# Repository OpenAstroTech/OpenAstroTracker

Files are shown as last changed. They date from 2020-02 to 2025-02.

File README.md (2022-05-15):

# The OpenAstroTracker:



https://youtu.be/9MNLAIyqGoA

A cheap 3D printed tracking, GoTo and autoguiding mount for DSLR astrophotography.

# [OpenAstroTracker Kits Now Available!](https://shop.openastrotech.com/products/openastrotracker-diy-kit)

# Links
 - [Software](https://github.com/OpenAstroTech/OpenAstroTracker/releases)
 - [Reddit](https://www.reddit.com/r/OpenAstroTech/)
 - [Discord](https://discord.gg/TmEfSNaBnB)
 - [Guides](https://www.reddit.com/r/OpenAstroTech/comments/gc4pmr/all_current_guides/)
 - [Wiki](https://wiki.openastrotech.com/)
 - [OpenAstroGuider](https://www.thingiverse.com/thing:4181640) Autoguiding Addon
 - [Community-made Addons](https://www.thingiverse.com/openastrotech/collections/things-for-the-openastrotracker) I'll add things to this Collection, if you made something, send me a message.
 - [My Images](https://www.instagram.com/fabianuehleke/)
 - [Community Images](https://www.flickr.com/groups/14697674@N24/)

##

**Use the [Printed Parts Chooser](https://docs.google.com/spreadsheets/d/1uDw7Jag2HRKztMPO7b06qFRg1eezGeb0IxJh84-QEao/edit?usp=sharing)**

# Like this Project?
**[Buy me and the devs a coffee!](https://www.paypal.com/donate/?hosted_button_id=HMY3H3PTGPFXN)**

If you would be interested in buying the tracker as a printed kit, head over to [this site](https://openastrotech.com/products/)

##

# Check out our [Wiki](https://wiki.openastrotech.com/) for all the guides!

This is the Repo for CAD and STL files. The other Repo's are:
 - [/OpenAstroTracker-Firmware](https://github.com/OpenAstroTech/OpenAstroTracker-Firmware) for OAT Arduino Firmware
 - [/OpenAstroTracker-Desktop](https://github.com/OpenAstroTech/OpenAstroTracker-Desktop) for OAT ASCOM and OATcontrol
 - [/OpenAstroTracker-Addons](https://github.com/OpenAstroTech/OpenAstroTracker-Addons) for OAT Hardware addons 
 - [/OpenAstroTracker-Apps](https://github.com/OpenAstroTech/OpenAstroTracker-Apps) (WIP) Mobile Apps

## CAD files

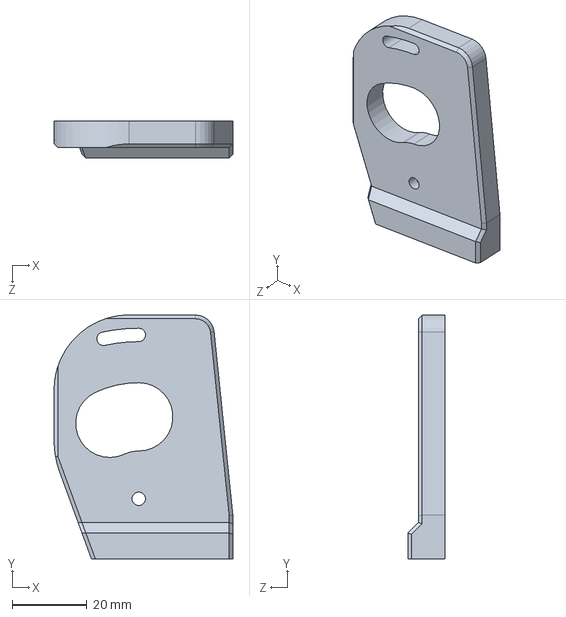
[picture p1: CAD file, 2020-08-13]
CAD/Solidworks/16_DEC_motor_mount_v8_low_NEMA14.SLDPRT
47.9 x 65.4 x 10.0 mm

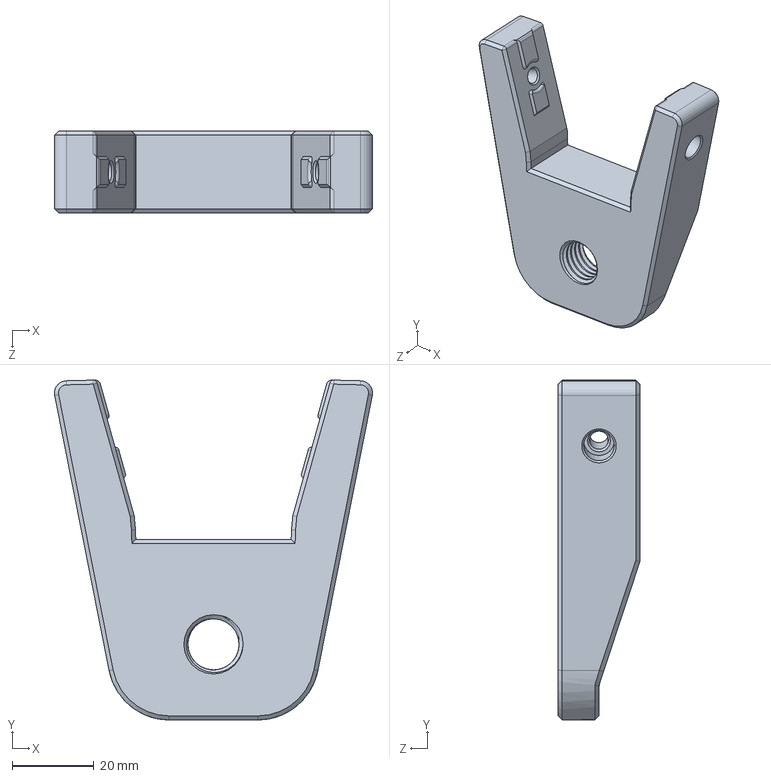
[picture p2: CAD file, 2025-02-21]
CAD/Solidworks/2020base/M14_mount_rear_2020base_v4.SLDPRT
77.8 x 83.2 x 20.0 mm

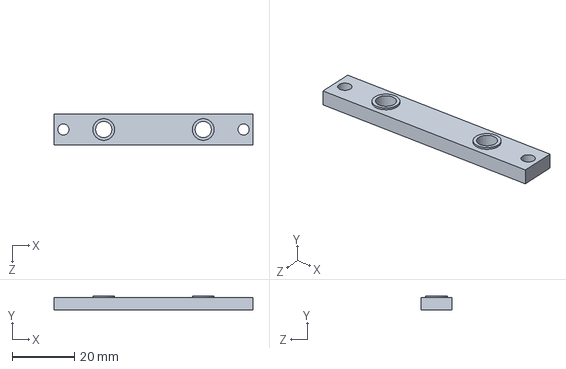
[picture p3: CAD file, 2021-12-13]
CAD/Solidworks/All Latitudes/16.1_DEC_idler_bracket_v1_NEMA.SLDPRT
64.0 x 4.50 x 10.0 mm

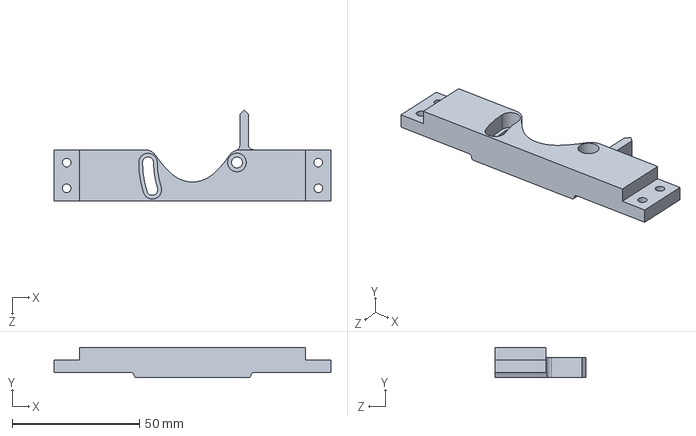
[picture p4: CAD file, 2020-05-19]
CAD/Solidworks/Printed Base & Printed Camera mount/For 200x200 printers/22_RAmotor_mount_low_v4_200x200.SLDPRT
109.0 x 12.0 x 35.9 mm

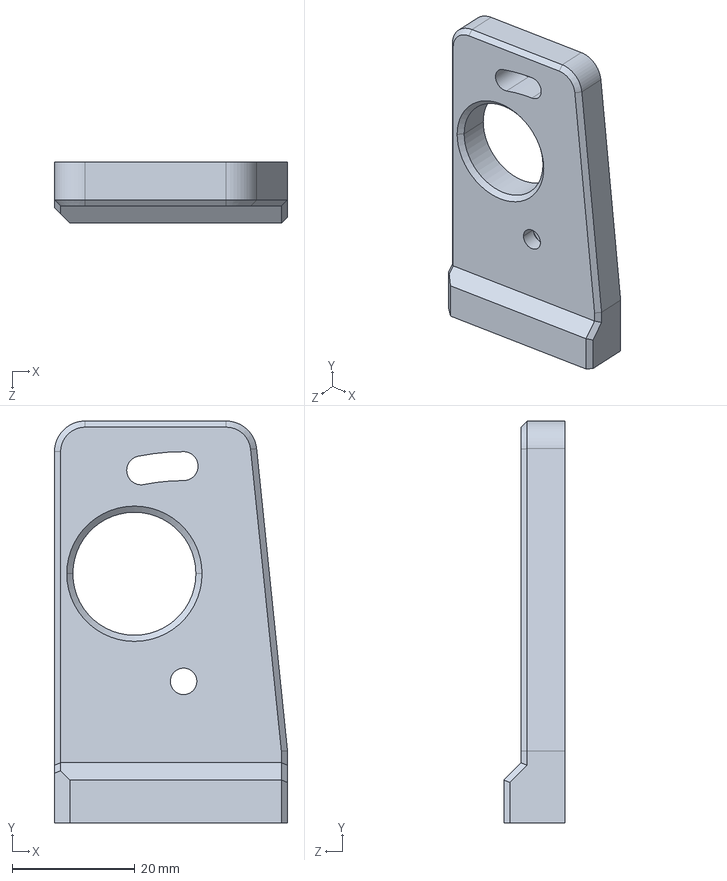
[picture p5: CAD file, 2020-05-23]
CAD/STEP/16_DEC_motor_mount_v7_low.step
37.9 x 65.4 x 10.0 mm

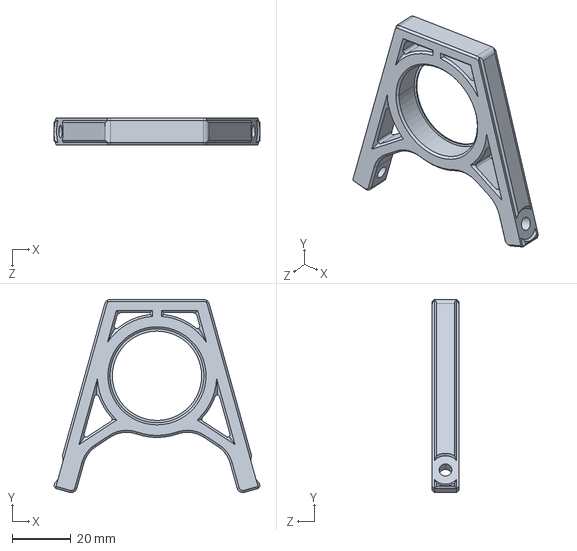
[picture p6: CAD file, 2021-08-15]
CAD/STEP/2020base/b2_level holder_31mm.STEP
69.9 x 65.6 x 9.00 mm

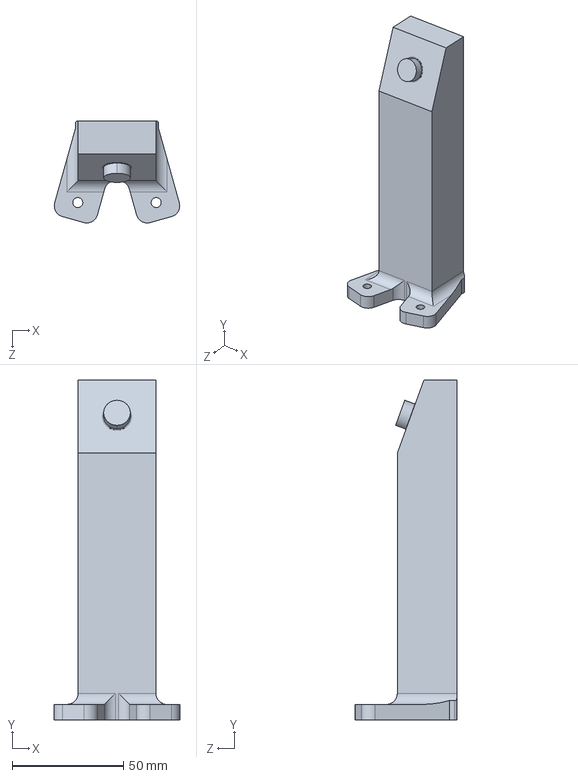
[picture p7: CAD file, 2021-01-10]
CAD/STEP/20deg/02_angle_20deg_2020base.step
56.5 x 152.9 x 45.8 mm

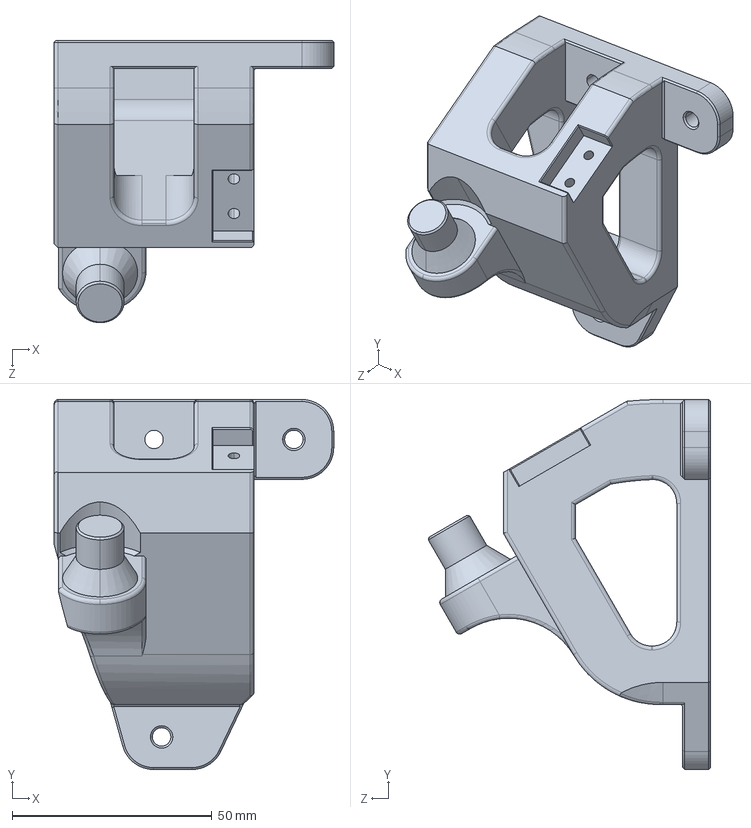
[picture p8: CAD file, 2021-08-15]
CAD/STEP/30deg/04_rollmount right_30°_v6_2020base.STEP
70.0 x 92.6 x 70.7 mm

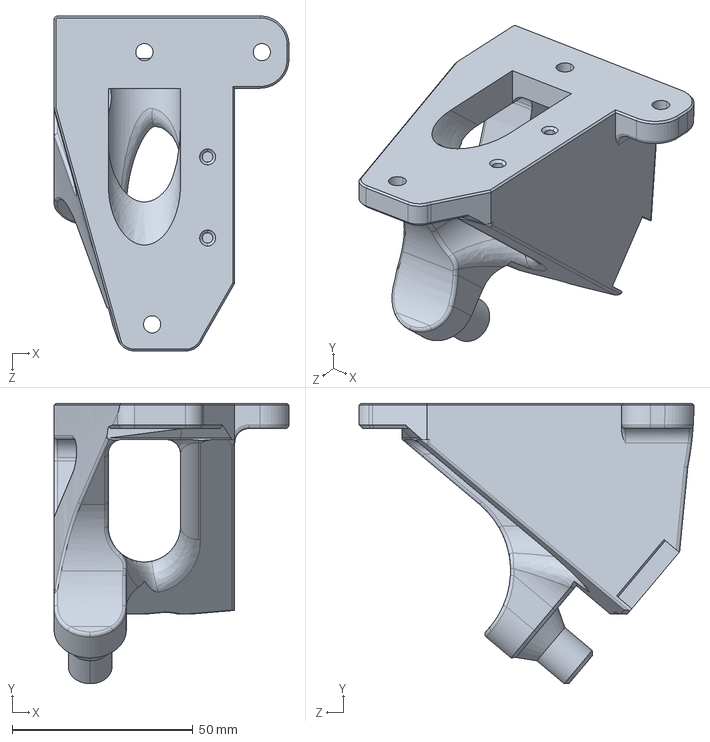
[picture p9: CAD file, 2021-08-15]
CAD/STEP/40deg/04_rollmount left_40°_v6_2020base.STEP
65.0 x 77.6 x 92.7 mm

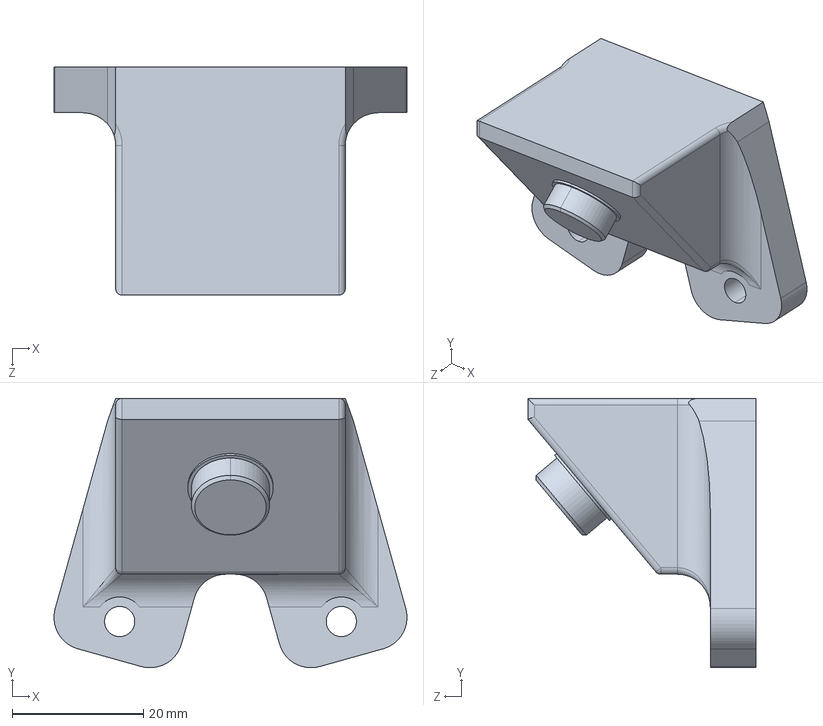
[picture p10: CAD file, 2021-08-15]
CAD/STEP/50deg/02_angle_50deg_v4_2020base.STEP
53.8 x 41.1 x 34.8 mm

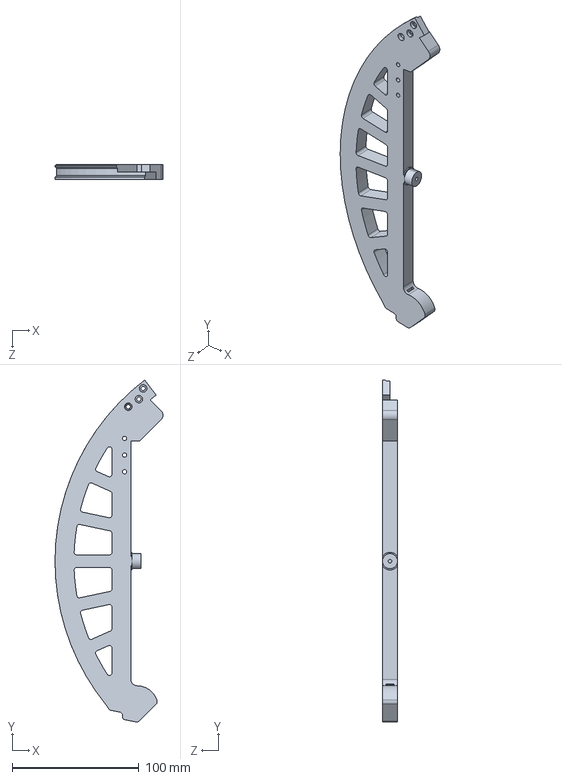
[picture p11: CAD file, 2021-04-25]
CAD/STEP/All Latitudes/For 200x200 Printers/06a_splitring_part1_v4f_200x200.STEP
85.3 x 270.3 x 12.0 mm

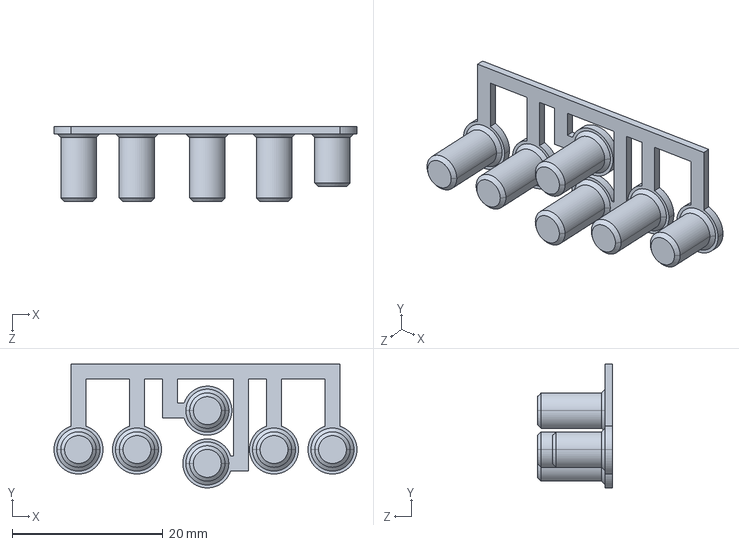
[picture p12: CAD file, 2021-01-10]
CAD/STEP/Arduino Mega Handcontroller/c4_buttons.step
40.2 x 16.4 x 10.0 mm

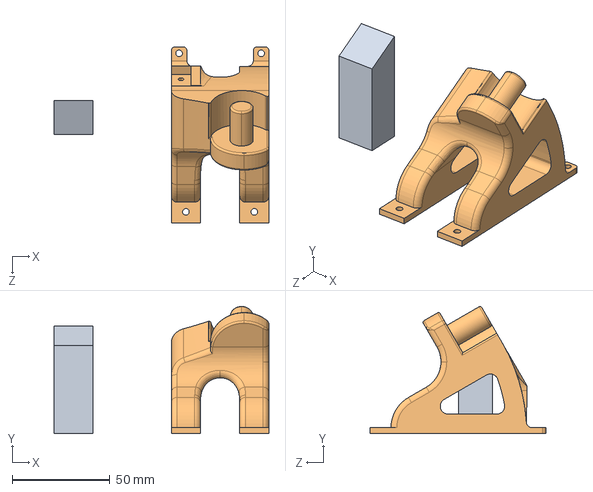
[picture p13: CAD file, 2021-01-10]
CAD/STEP/Printed Base & Printed Camera mount/04_rollmount left_30°_v3.step
110.0 x 65.0 x 90.3 mm

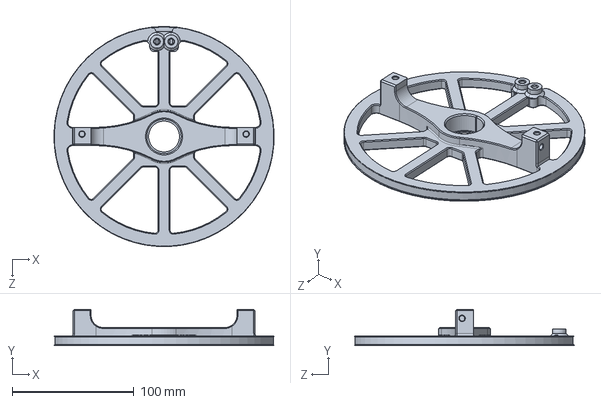
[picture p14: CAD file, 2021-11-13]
CAD/STEP/Universal mount/u3_drivedisc_DEC_unimount_v3_TI.STEP
181.0 x 30.0 x 181.2 mm

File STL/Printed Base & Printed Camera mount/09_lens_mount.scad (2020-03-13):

//$fn=10;

//lens_diameter = 62;

diam1 = 69.5;
diam2 = 69.5;
high1 = 6;


diam3 = 62.5;
diam4 = 62.5;
high2 = 25;

high3 = 0;
diam5 = 0;
diam6 = 0;

length = 30; //reduce this if needed

/*union() {
translate([0,0,20]) cube([(diam1/2)+5,100,10]);
mirror([1,0,0]) translate([0,0,20]) cube([(diam1/2)+5,100,10]);
mirror([0,1,0]) translate([0,0,20]) cube([(diam1/2)+5,100,10]);
mirror([1,0,0])mirror([0,1,0]) translate([0,0,20]) cube([(diam1/2)+5,100,10]);
}*/

difference (){
difference (){
difference (){
union (){
    cylinder (h=30,d=diam1+10,$fn=512);
    cube([67,15.5/2,30]);
    mirror([1,0,0]) cube([67,15.5/2,30]);
    mirror([0,1,0]) cube([67,15.5/2,30]);
    mirror ([1,0,0])mirror([0,1,0]) cube([67,15.5/2,30]);
}
}
union () {
translate([0,0,-0.001]) cylinder(high1+0.1,d1=diam1,d2=diam2,$fn=512);
translate([0,0,high1-0.01]) cylinder(high2+0.1,d1=diam3,d2=diam4,$fn=512);
translate([0,0,high1+high2-0.02]) cylinder(high3+0.1,d1=diam5,d2=diam6,$fn=512);
    
union() {
translate([0,0,length+0.001]) cube([(diam1/2)+4.2,100,100]);
mirror([1,0,0]) translate([0,0,length+0.001]) cube([(diam1/2)+4.2,100,100]);
mirror([0,1,0]) translate([0,0,length+0.001]) cube([(diam1/2)+4.2,100,100]);
mirror([1,0,0])mirror([0,1,0]) translate([0,0,length+0.001]) cube([(diam1/2)+4.2,100,100]);
}
    
}
}
cube([150,1,61],center=true);
translate ([67-15,5.9/2+4.45,15/2]) hex(5.9,5.9);
translate ([67-15,5.9/2+4.45,30-15/2]) hex(5.9,5.9);
translate ([-67+15,5.9/2+4.45,15/2]) hex(5.9,5.9);
translate ([-67+15,5.9/2+4.45,30-15/2]) hex(5.9,5.9);
translate([67-15,8,15/2]) rotate([90,0,0]) cylinder(h=20,d=3.4,$fn=512);
translate([67-15,8,30-15/2]) rotate([90,0,0]) cylinder(h=20,d=3.4,$fn=512);
translate([-67+15,8,15/2]) rotate([90,0,0]) cylinder(h=20,d=3.4,$fn=512);
translate([-67+15,8,30-15/2]) rotate([90,0,0]) cylinder(h=20,d=3.4,$fn=512);
translate([67-15,-3.95,15/2]) rotate([90,0,0])cylinder (h=5,d=5.8,$fn=512);
translate([67-15,-3.95,30-15/2]) rotate([90,0,0])cylinder (h=5,d=5.8,$fn=512);
translate([-67+15,-3.95,15/2]) rotate([90,0,0])cylinder (h=5,d=5.8,$fn=512);
translate([-67+15,-3.95,30-15/2]) rotate([90,0,0])cylinder (h=5,d=5.8,$fn=512);
}


module hex(wid,height){
hull(){
cube([wid/1.7,wid,height],center = true);
rotate([0,120,0])cube([wid/1.7,wid,height],center = true);
rotate([0,240,0])cube([wid/1.7,wid,height],center = true);
}
}

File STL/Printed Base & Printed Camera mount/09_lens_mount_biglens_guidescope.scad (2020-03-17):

//$fn=10;

//lens_diameter = 62;

diam1 = 69.5; //[0:0.1:120]
diam2 = 65.5; //[0:0.1:120]
high1 = 6; //[0:0.1:30]


diam3 = 62.5; //[0:0.1:120]
diam4 = 62.5; //[0:0.1:120]
high2 = 25; //[0:0.1:30]

diam5 = 0; //[0:0.1:120]
diam6 = 0; //[0:0.1:120]
high3 = 0; //[0:0.1:30]

/* [Hidden] */
dmax = max(diam1,diam2,diam3,diam4,diam5,diam6);
gy = sqrt(max(dmax*dmax/4-41.9*41.9,20*20))+8;
gx_1 = sqrt((dmax/2+2.5)*(dmax/2+2.5)-gy*gy);
gx_2 = sqrt((dmax/2+2.5)*(dmax/2+2.5)-7.5*7.5);
gx_3 = max(sqrt((dmax/2+5)*(dmax/2+5)-7.5*7.5),57.1);

$fn=512;

difference (){
difference (){
difference (){
union (){
    cylinder (h=30,d=diam1+10);
    cube([91.3,15.5/2,30]);
    mirror([1,0,0]) cube([91.3,15.5/2,30]);
    mirror([0,1,0]) cube([91.3,15.5/2,30]);
    mirror ([1,0,0])mirror([0,1,0]) cube([91.3,15.5/2,30]);
    translate([0,0,6]) linear_extrude(height=18) polygon(points=[[-gx_1,-gy],[-55.1,-gy],[-57.1,-gy+2],[-gx_3,-7.49],[-gx_2,-7.49]]);
    mirror([1,0,0]) translate([0,0,6]) linear_extrude(height=18) polygon(points=[[-gx_1,-gy],[-55.1,-gy],[-57.1,-gy+2],[-gx_3,-7.49],[-gx_2,-7.49]]);
}
}
union () {
translate([0,0,-0.001]) cylinder(high1+0.1,d1=diam1,d2=diam2);
translate([0,0,high1-0.01]) cylinder(high2+0.1,d1=diam3,d2=diam4);
translate([0,0,high1+high2-0.02]) cylinder(high3+0.1,d1=diam5,d2=diam6);
}
}
cube([200,1,61],center=true);
translate ([91.3-15,5.9/2+4.45,15/2]) hex(5.9,5.9);
translate ([91.3-15,5.9/2+4.45,30-15/2]) hex(5.9,5.9);
translate ([-91.3+15,5.9/2+4.45,15/2]) hex(5.9,5.9);
translate ([-91.3+15,5.9/2+4.45,30-15/2]) hex(5.9,5.9);
translate([91.3-15,8,15/2]) rotate([90,0,0]) cylinder(h=20,d=3.4);
translate([91.3-15,8,30-15/2]) rotate([90,0,0]) cylinder(h=20,d=3.4);
translate([-91.3+15,8,15/2]) rotate([90,0,0]) cylinder(h=20,d=3.4);
translate([-91.3+15,8,30-15/2]) rotate([90,0,0]) cylinder(h=20,d=3.4);
translate([91.3-15,-3.95,15/2]) rotate([90,0,0])cylinder (h=5,d=5.8);
translate([91.3-15,-3.95,30-15/2]) rotate([90,0,0])cylinder (h=5,d=5.8);
translate([-91.3+15,-3.95,15/2]) rotate([90,0,0])cylinder (h=5,d=5.8);
translate([-91.3+15,-3.95,30-15/2]) rotate([90,0,0])cylinder (h=5,d=5.8);
translate([-47,-gy+3,15]) cube([10.2,10,8.2],center=true);
translate([47,-gy+3,15]) cube([10.2,10,8.2],center=true);
}


module hex(wid,height){
hull(){
cube([wid/1.7,wid,height],center = true);
rotate([0,120,0])cube([wid/1.7,wid,height],center = true);
rotate([0,240,0])cube([wid/1.7,wid,height],center = true);
}
}

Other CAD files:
CAD/STEP/All Latitudes/11.1_DEC_idler_bracket_v1_NEMA.STEP
STL/2020 Base/b2_level holder_60mm.STL
STL/20deg/04_rollmount right_20°_v5_2020base_TI.STL
STL/30deg/04_rollmount right_30°_v6_2020base_TI.STL
STL/Printed Base & Printed Camera mount/09_lens_mount_biglens.scad
CAD/STEP/03_polemount_6801.step
CAD/STEP/10.1_pole_v2.step
CAD/STEP/10_pole_20deg.step
CAD/STEP/10_pole_30deg.step
CAD/STEP/10_pole_40deg.step
CAD/STEP/10_pole_50°.step
CAD/STEP/10_pole_50°_v2.step
CAD/STEP/11a_splitring_part1_timingbelt.step
CAD/STEP/11a_splitring_part1_v2.step
CAD/STEP/11b_splitring_part2_v2.step
CAD/STEP/11c_splitring_part3_timingbelt.step
CAD/STEP/11c_splitring_part3_timingbelt1.step
CAD/STEP/11c_splitring_part3_v2.step
CAD/STEP/16_DEC_motor_mount_v6.step
CAD/STEP/16_DEC_motor_mount_v6_low.step
CAD/STEP/2020base/16_NEMA_electronicsbox.step
CAD/STEP/2020base/16_NEMA_electronicsbox_lid.step
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

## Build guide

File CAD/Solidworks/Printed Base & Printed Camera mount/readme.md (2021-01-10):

Numberation on these parts may differ from the STLs

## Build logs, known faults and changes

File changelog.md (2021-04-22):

# Changelog

## Parts
22.04.2021
 - Updated 14_RAmotor_mount_NEMA_down to v4, adding adjustment for belt tension and making _up obsolete. 
 - Added 14_RAmotor_mount_NEMA_down_SngleRAring_v4 for the single piece RA Rings.
 - Updated 05_pole to v5, adding stoppers for upcoming sensorless homing with TMC2209 builds.

20.05.2020
 - see [this post](https://www.reddit.com/r/OpenAstroTech/comments/gnjsvu/a_whole_bunch_of_updated_parts/)

10.04.20
 - updated the files for 200x200 printers with the v2 ring

17.03.2020

 - updated parts 6a,b,c and 14 to v2
 - added klwill1192's lens adapter for big lenses with the guidescope
 Please see the [update post](https://www.reddit.com/r/OpenAstroTech/comments/fkcdho/improvements_to_the_splitring_design_and/) 

13.03.2020

 - added adaptions of parts 11 and 14 (the motor mounts) with the addendum "_low". These will fit with purchased GT2 pulleys.
 - updated the lens ring SCAD. It has a new value "length" for lenses that have little space to mount it.

10.03.2020

 - added 01a, 01b, 06a, 06c adaptions to fit into 200x200 printers
 - updated part 10 to fit tighter with the camera mount, part 08

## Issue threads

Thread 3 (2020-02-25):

SCAD files

BenJuan26, 2020-02-25:
This repo doesn't seem to have the SCAD files mentioned in the readme. I do see that they're on Thingiverse. Should they be added here?

BenJuan26, 2020-02-25:
Found them, in `/STL/All latitudes`. Just another reminder that GitHub's search is garbage.

Closed 2020-02-25.

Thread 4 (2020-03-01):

Assemply instructions

crami, 2020-03-01:
Hi
Could you probably post some assembly instructions or some close-up Photos of your assembled OpenAstroTracker to make assembly easier?

Thanks
  Matthias

threalboss, 2020-03-06:
He is currently working on revising the build guide. Keep up to date on r/openastrotech https://www.reddit.com/r/OpenAstroTech/

OpenAstroTech, 2020-03-28:
have been added

Closed 2020-03-28.

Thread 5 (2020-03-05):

Arduino Code

ztwillis, 2020-03-05:
In the Calculations file in the Arduino code the pins were different than those in Init:
I believe this should be what it reads:

if (DECheat == 1) {
  stepperDEC.enableOutputs();
  digitalWrite(15, HIGH);
  digitalWrite(16, HIGH);
  digitalWrite(17, HIGH);
  digitalWrite(18, HIGH);

Also when I enter my HA from based on Polaris in in stellarium the declination axis(initial position starting perpendicular to RA axis) goes nearly 180 degrees when I enter my HA and go to the Polaris tab and select it.  Thanks in advance!

OpenAstroTech, 2020-03-05:
> different than those in Init

oh right thanks, i changed it

> goes nearly 180 degrees when I enter my HA and go to the Polaris tab and select it

Thats weird, that cant happen unless you entered some coordinates before using the POL menu

ztwillis, 2020-03-05:
Honestly it's probably user error, mostly I just wanted to let you know about the Arduino code, thanks for the quick response and all of the work you're doing!

Closed 2020-03-05.

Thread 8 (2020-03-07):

DEC guiding imprecise

OpenAstroTech, 2020-03-07:
because

a) DEC stepper not precise enough. Could be improved by half-stepping

b) Declination axis unbalanced with guidescope attached. Could be solved by adding counterweights

OpenAstroTech, 2020-03-19:
After further testing, i dont think DEC guiding will ever be precise. Even a single halfstep is roughly one arcmin of movement which is really borderline for ~200mm lenses but not precise enough for higher focal lengths

OpenAstroTech, 2020-08-20:
DEC guiding is working with NEMA stepper on DEC axis

Closed 2020-08-20.

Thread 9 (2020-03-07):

No guidescope attachment for _biglens

OpenAstroTech, 2020-03-07:

klwill1192, 2020-03-16:
Here's my first cut at adding the guide scope mount to the lens mount.

[09_lens_mount_biglens_guidescope.zip](https://github.com/OpenAstroTech/OpenAstroTracker/files/4335575/09_lens_mount_biglens_guidescope.zip)

OpenAstroTech, 2020-03-17:
added!

Closed 2020-03-17.

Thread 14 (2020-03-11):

Button

tomv79, 2020-03-11:
The left button does not switch throught the menues.
It has the same effect as the down button.
Sometimes the left button switches the menue.

OpenAstroTech, 2020-03-11:
Go to the second tab of the code "a_inits" and find line 36 "if (adc_key_in < 600)  return btnLEFT;"

Try if changing the value in that line to 700 or 800 fixes it

tomv79, 2020-03-11:
Yes the left button now works.
But the select button seem to be the left now.

OpenAstroTech, 2020-03-11:
Try increasing its value in the code till it works

tomv79, 2020-03-12:
I have make following changes that works for me well!!

if (adc_key_in > 1000) return btnNONE;
  if (adc_key_in < 20)   return btnRIGHT;
  if (adc_key_in < 150)  return btnUP;
  if (adc_key_in < 300)  return btnDOWN;
  if (adc_key_in < 500)  return btnLEFT;
  if (adc_key_in < 700)  return btnSELECT;

now the keys works fine!

OpenAstroTech, 2020-03-13:
Great! I'll mention this in the upcoming troubleshooting guide, i think some of the LCDs need different values.

Gonna close this

Closed 2020-03-13.

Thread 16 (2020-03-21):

BUG : RASteps not being correctly converted to float in c_buttons.ino

EorEquis, 2020-03-21:
Current line 8 is
`onehour = (float(RAsteps / 288)) * RevSteps;`

Which leave RASteps as an int  (this produces /u/mxpwr60's comment that 288 is the "lower limit" as seen [here](https://old.reddit.com/r/OpenAstroTech/comments/fmiwwz/calibration/), since dividing any int < 288 by 288 returns 0.

It also results in the RA Rate being impossible to set as described in the setup/calibration instructions, since only RASteps values that are multiples of 288 (288, 576, etc) will produce any change in the value of onehour.

I believe code should be
`onehour = (float(RAsteps) / 288) * RevSteps;`

Have made this change in my mount, and see RA calibration results as expected.

OpenAstroTech, 2020-03-28:
forgot to close it

Closed 2020-03-28.

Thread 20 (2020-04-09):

Use common 608 bearings

christoph1703, 2020-04-09:
It would be great to use the common 608 bearings instead of the 12mm ID bearings required now. The price and availability are much better.
I modified the stl files myself before printing, but I don't have access to SolidWorks, so I can't contribute updated files. I'd be happy to help otherwise if needed.
Thanks for providing this thing for free!

andre-stefanov, 2020-06-11:
You can use the .step files for the remixing and later export if for solidworks in e.g. Fusion 360

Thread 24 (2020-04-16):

missing CAD Files

regularUsername, 2020-04-16:
STEP and Solidworks files for **02_angle_30deg** are missing

OpenAstroTech, 2020-04-16:
I have no idea how that happened, but i added them. Thanks!

Closed 2020-04-16.

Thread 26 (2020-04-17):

V1.6 not compiling

raminnobari, 2020-04-17:
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
V1.6. not compiling properly. Errors are located in "d-calulation" and "f-printout" files.
I have no issues with v1.4.5 ...

Am I doing something wrong ?!

raminnobari, 2020-04-17:
1.6.25 compiles just fine. "d-calulation" and "f-printout"  are already gone.

OpenAstroTech, 2020-04-17:
There were accidentally some wrong files in the initial upload for 1.6.25. I reuploaded the code, it should work now with the latest release

raminnobari, 2020-04-17:
perfect

Closed 2020-04-17.

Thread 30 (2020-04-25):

GoTo not working for negative DEC

StandaB, 2020-04-25:
Navigating to POI M42 Orion nebula moves OAT to DEC 90°22' instead of -5°22'. It seems that in _struct PointOfInterest_ using "byte degreeDEC;" is problematic since _byte_ is unsigned. Using _int degreeDEC_ solved this for me

nice project though. I made a slight modification to use A4988 stepper drivers with microstepping to see if it is possible to have smoother tracking. Just waiting for a clear sky now :)

andre-stefanov, 2020-12-13:
Thx! Fixed in e4f2c06743984873fc060b9975149918a24d1c0c

Closed 2020-12-13.

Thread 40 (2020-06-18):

LCD Keypad buttons misbehaving

scoutstang, 2020-06-18:
I just wanted to report an issue I ran into getting my new OAT build up and running. With the electronics hooked up and the latest firmware loaded, some of my buttons were misbehaving. Both the Left and Select buttons were acting like Select and the Down button was acting like Left.

I was able to enable LCD_BUTTON_TEST in Globals.hpp to see the output of my buttons and then change the cutoff values accordingly in the checkKey () part of Utility.hpp. I changed the cutoffs to 50/300/500/700/950. Now the buttons respond correctly.

For the record, I am using firmware 1.7.04 with a Mega 2560 clone (Sunfounder) and the DFRobot LCD Kaypad Shield v1.1. They key diagnostic is reporting: 0-Right, 205-Up, 405-Down, 623-Left, 824-Select, and 1023-None.

Looking forward to clear skies so I can try it out soon!

andre-stefanov, 2020-12-13:
Thanks for that information. We are indeed seeing this issues from time to time because the LCD Keypad shields seem to differ in terms of voltages on each button. Our proposed fix is exactly what you did. I will add this information to the wiki so maybe someone can look it up if he faces same problem.

Closed 2020-12-13.

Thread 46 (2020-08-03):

OATcontrol crashing on startup

BenJuan26, 2020-08-03:
I've downloaded the latest release and extracted OATcontrol. When I try to run `OATControl.exe`, it crashes instantly; no error message, no error report, etc. I attached Visual Studio to the `.exe` and got a bit more information. It seems to be a registry access permission denied. Here is the stack trace:

```
 at ASCOM.Utilities.RegistryAccess.OpenSubKey(RegistryKey ParentKey, String SubKeyName, Boolean Writeable, RegWow64Options Options)\r\n   at ASCOM.Utilities.RegistryAccess.NewCode(Boolean p_IgnoreChecks)
```

And the accompanying message is:

```
OpenSubKey: Exception encountered opening key - Result: 0x5
```

I can probably build from source but I thought it important to point out that the release is crashing for me.

ClutchplateDude, 2020-08-03:
Do you have the latest ASCOM installed (I think 6.2) ?

BenJuan26, 2020-08-03:
That was the issue. I was getting my computers confused and didn't have ASCOM installed on this one. Still, catching the exception would probably be a good idea so that other people know what the problem is.

ClutchplateDude, 2020-08-03:
I think this might be too early to catch an exception. The program won't even start up if the dependencies are missing. Did you have to see any OATControl code in the stack when you looked at that exception?

BenJuan26, 2020-08-03:
> I think this might be too early to catch an exception.

I think you're right. There was very little info available, and I didn't see an OATcontrol file or line number mentioned anywhere. It complained about one of the constructors throwing an exception, but I don't recall whether it was OATcontrol-specific or some internal .NET class. I don't have the report handy anymore, and now that I've installed ASCOM I won't be able to reproduce it.

ClutchplateDude, 2020-08-03:
My problem also :-)

Closed 2020-08-03.

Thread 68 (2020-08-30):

Wrong Serial interface for DEC?

stone17, 2020-08-30:
https://github.com/OpenAstroTech/OpenAstroTracker/blob/d383d151e34142fe88fd5ae8a6d664c53c0af1c6/Software/Arduino%20code/OpenAstroTracker/Configuration_pins.hpp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

This should be Serial2?

My DEC motor doesnt work properly if this is set to Serial3.

pay4nothing, 2020-10-23:
Hi @Stone17,

thank you for your comment. I just had a weird behavor of the DEC axis with slipping and non holding the position. I fixed this to Serial2 and my problem was solved. So thank you!

andre-stefanov, 2020-10-23:
@ClutchplateDude this really looks like a type. I just wonder why it did not cause issues for e.g. @OpenAstroTech since the this change was done 3 months ago with [v1.8.02](https://github.com/OpenAstroTech/OpenAstroTracker/commit/308a0b3f82951cc9539fa4a7019a85a127707cfb)

pmneo, 2020-12-03:
RA and DEC can be both on Serial3. The have different adresses: 0b00 for RA (with MS0 = LOW and MS1 = LOW) and 0b01 for DEC (with MS0 HIGH and MS1 LOW) (https://wiki.openastrotech.com/wiki/NEMA_Wiring#TMC2209)

CS

andre-stefanov, 2020-12-13:
The issue was fixed by adapting the comment. Be aware that the most recent version of this file looks different because it is using separate pin number definitions now (to also allow SoftwareSerial).

Closed 2020-12-13.

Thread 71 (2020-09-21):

[Arduino] Implement Level LX200 commands

ClutchplateDude, 2020-09-21:
Add some LX200 extensions to allow query of Digital Level data

ClutchplateDude, 2020-10-07:
Fixed in V1.8.33

Closed 2020-10-07.

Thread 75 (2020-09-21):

[Arduino/LCD] Allow button press at boot to reset EEPROM

ClutchplateDude, 2020-09-21:

ClutchplateDude, 2020-10-06:
Fixed in 1.8.24

Closed 2020-10-06.

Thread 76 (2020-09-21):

[Arduino] Implement Park position different from Home

ClutchplateDude, 2020-09-21:
Stop the DEC from crashing into RA ring on power down.
Store step offset from home in EEPROM.

ClutchplateDude, 2020-10-12:
Implemented in V1.8.35

Closed 2020-10-12.

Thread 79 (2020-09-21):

[Arduino] Configure NEMA pins for ESP32

ClutchplateDude, 2020-09-21:

chatainsim, 2020-11-19:
Hello,
Is the ESP32+NEMA code release yet ? Or do we have tu use arduino mega/uno for now with the nema motor ?

Thanks

andre-stefanov, 2020-11-19:
Esp32 already supports nemas on develop branch. Uno was removed from supported devices due to low memory.

Closed 2020-11-19.

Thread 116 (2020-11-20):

LHolder file size / export settings

0x4d4e, 2020-11-20:
While it is probably not an issue regarding the print, I noticed that the Lholder stl files are vastly different in file size (15MB (!) vs 500KB) between left and right. Loading the file into Cura took considerably longer for me, otherwise I noticed no difference. Is it just due to different stl export settings?

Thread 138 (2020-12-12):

Problem with printed parts

garnek1605, 2020-12-12:
Hello,
first of all - thanks for that great project !
I'm still printing parts and found 2 issues
1. \OpenAstroTracker-master\CAD\STEP\03_polemount_6801_v2.step - this part has 0,5 mm bottom instad of around 5 mm. Easy to fix just need to extrude the bottom to correct hight.
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

2.\OpenAstroTracker-master\CAD\STEP\11a_splitring_part1_v4.step
\OpenAstroTracker-master\CAD\STEP\11b_splitring_part2_v4.step
\OpenAstroTracker-master\CAD\STEP\11b_splitring_part2_timingbelt.step
This is more complicated. 2 Holes are missaligned (on the outer parts) and there is a problem with the perimeter around the joint. A picture is worth 1000 words.

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

intercipere, 2020-12-12:
Hey,

for no. 1 i assume you mean the side marked with "2" in your picture? that is supposed to be shaped like that, arguably a bit thin but its correct.

For no. 2 you have the wrong middle part loaded, this one is the correct one: https://github.com/OpenAstroTech/OpenAstroTracker/blob/master/CAD/STEP/11b_splitring_part2_v4.step
(i know, i know, theres a file cleanup coming up :)

garnek1605, 2020-12-12:
Part 1, the problem I had was the bed adhesion, this 0,5 mm zones got ripped apart or deformed after I broke it off the bed. The "old" version of that part was 20mm thick. My idea was to extrude the new part thicker so i can break it off the bed in one piece. Is there going to be a problem of colliding with something i know nothing about yet ?

Part 2 solved, it will remain a mystery for me, how I might have missed it.Thanks for the help.
+

Closed 2020-12-12.

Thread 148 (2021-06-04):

Wikifactory open hardware community welcomes OpenAstroTracker!

sandina, 2021-06-04:
Hey OpenAstroTech team!

Just recently, a community member of Wikifactory recommended your Project to join our collaboration platform for open hardware - with a community of over 100,000 designers, engineers and hardware innovators working on over 5K hardware and product innovation projects.

I am co-founder of Wikifactory myself and agree that the greater community on Wikifactory and especially our space and astronomy enthusiasts, would not only learn a lot from your project but would like the chance of contributing and building upon your amazing work.

As a social platform for collaborative product development, we definitely were inspired tools like Github and we focused on building a collaboration infrastructure built for product design from the ground up.

A few months ago, we launched an Import from Github feature to make it very easy to bring projects that already exist on Github into Wikifactory in just a few minutes.

I went ahead and imported your project to see how it would look, and whilst it is not listed for the broader community - I have the chance to show you how it would result! Take a look! https://wikifactory.com/@botler/the-openastrotracker

I would love your feedback. My hopes is that we could transfer the project to you so that it can be listed on our Platform for our community to find and engage with.

We have built Wikifactory for projects like yours, so I would definitely care to know what you think and I would even suggest that we show you around in a Demo too!

At the heart of this message is that I would hope to be able to see your project evolve and grow with our community.

cameronswinoga, 2021-06-05:
@sandina Thanks for reaching out, wififactory looks interesting. We've had an internal discussion and decided that our current CAD workflow works well enough for our needs, but we will keep wikifactory in mind as a future platform option. :)

sandina, 2021-06-06:
Thanks @cameronswinoga, I can totally understand, achieving a workflow like you have done is a feat and I can understand that a shift could compromise that. Really do hope to see you guys build something on Wikifactory one day, do let me know and I would be happy to give you guys a show around. I like to follow teams like yours, because it is what inspires us in building Wikifactory.

We ultimately want to understand what it takes for real-time CAD collaboration online and how that can enable open source innovation in hardware and physical products. So I thought to share with you a glimpse of what i mean for future reference - https://wikifactory.com/@botler/the-openastrotracker/file/CAD/STEP/20deg/04_rollmount%20right_20%C2%B0_v5_2020base.step

Would you want me to take the project down from Wikifactory? It currently is under a Public Domain Profile we call Botler, attributing back to this repository and recognising you as authors. I can understand that you might not want to maintain the project on Wikifactory, but just wanted to triple check whether you would also like to remove the forked project from the Wikifactory platform.

Look forward to seeing your progress, and thanks!

cameronswinoga, 2021-06-06:
@sandina yes please remove the project, thanks for checking with us :)

Closed 2021-06-05.

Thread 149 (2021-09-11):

Improvements to M14_mount_rear_2020base_v2

JakobPetersson, 2021-09-11:
In my experience, the M14_mount_rear_2020base_v2-part does not fasten completely in its  current design.
It will shift vertically depending on pressure, rotating around the M4-screws.

Possible improvements:
1. Add the raised middle "band" that fits into the alu-profile.
2. Two M4 screws on each side, instead of just one.

Both of these design choices already are in the other 2020base-parts and stops them from rotating in relation to the alu-profile.
Example: M14_mount_right_2020base and M14_mount_left_2020base.

I cannot find information about how to contribute changes to the 3D parts to make these changes.
I can just assume a PR should include changes to the Solidworks,.step and .stl-files and I will try to make these changes if no one else beats me to it.

---
Closing issue due to opening a PR instead. Easier to discuss there.

Closed 2021-09-11.

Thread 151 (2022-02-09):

Bubble level holder diameter is 65mm but shopping list linked item is 60mm in diameter.

JJ-White, 2022-02-09:
I've ordered the bubble level straight through the Aliexpress link on the shopping list page (https://wiki.openastrotech.com/en/OpenAstroTracker/ShoppingList) and now that I've printed the holder I find out that the holder is made for a bubble level with a diameter of 65mm. The shopping list itself still lists the 65mm version but maybe the listing itself changed? I'll probably hot glue it in for now as the level can be stuck through the smaller hole but won't stay in place.

Could someone make an updated model for the 60mm version, as I can assume more people have bought this version?

intercipere, 2022-02-09:
Hey, i added a holder for 60mm bubble levels

https://github.com/OpenAstroTech/OpenAstroTracker/blob/master/STL/2020%20Base/b2_level%20holder_60mm.STL

Closed 2022-02-09.

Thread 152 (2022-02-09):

When printing the threaded insert parts (TI), why are there still a bunch of non-TI holes?

JJ-White, 2022-02-09:
As you might gather from my previous issue I've been printing the parts for the base, and I've used the OAT Part chooser v1.5.1 to select the parts to be printed. I've chosen the option for threaded inserts, but after printing the base I notice only the holes that mount the 14_RAmotor_mount_NEMA_down bracket on the left and right rollmounts have the right dimensions for the inserts. The 4 holes to mount the rollmounts to the base all have non-TI dimension, and so does the hole on the bottom of the 02_angle_2020base part, which doesn't even have a TI version.

I haven't printed any of the moving assembly yet, but I'm wondering why not all places where bolts thread into plastic have been changed?

crashmaxx, 2022-02-10:
I agree with using inserts everywhere possible.

I'd be willing to make the files if someone can help put together a list of parts that need to have TI versions made.

JJ-White, 2022-02-10:
So far the parts I found with missing TI changes are:
- 04_rollmount <left/right>_<degrees>_v6_2020base_TI.STL - These still have normal sized holes on the bottom of the parts, but are the correct size for the RA motor bracket mount.
- 02_angle_<degrees>deg_v4_2020base.STL - This part needs a TI version where the size of the hole in the bottom is increased.

I'm still in the process of printing the parts not in the base, but so far they all seem to have a correct TI version. I assume only the screws hidden on the bottom were overlooked when making the TI parts.

JJ-White, 2022-02-11:
Wouldn't it make more sense to also make them threaded? If you're printing the TI parts you will already have threaded inserts at hand, and IMO they make the build feel a lot higher quality. But I agree it's definitely not a big deal.

DRA6N, 2022-02-12:
> Wouldn't it make more sense to also make them threaded? If you're printing the TI parts you will already have threaded inserts at hand, and IMO they make the build feel a lot higher quality. But I agree it's definitely not a big deal.

You can slowly enlarge the holes with a drill bit and insert your own TI's.

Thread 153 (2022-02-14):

[Printed parts] What is the thread profile on the M14 holes?

JJ-White, 2022-02-14:
I've designed my own M14 bolt in Fusion 360 to use with the OAT, but after printing without any added clearance it fits very loosely in the M14 threaded holes of the OAT and wobbles around. I've used ISO Metric Profile M14x2 when creating my bolt, does the model use a different profile?

Update: I've overlayed the STL on my bolt in Fusion and the profile seems to be the same. There does seem to be a massive 0.4mm clearance on each side, or 0.8mm in total. Is this intentional?

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

JJ-White, 2022-02-14:
I've expanded the M14 thread of my bolt in Fusion using trial and error, and I've landed at around 0.13mm all round, so 0.26mm extra width in total for a tight fit.

Closed 2022-02-14.

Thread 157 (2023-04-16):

Degree symbol in filename causing Klipper to crash when starting a print job

daniel-gallagher, 2023-04-16:
I encountered a frustrating issue when trying to print [04_rollmount left_30°_v6_2020base_TI.STL](https://github.com/OpenAstroTech/OpenAstroTracker/blob/master/STL/30deg/04_rollmount%20left_30%C2%B0_v6_2020base_TI.STL) where Klipper would crash with an SD card error message when attempting to print. I chased the issue for a while before I discovered it was the `°` symbol in the filename that was causing Klipper to crash (Unicode character issue?). Once I replaced that symbol with `deg`, like most of the other file names, I was able to print successfully. There is also a space in the filename that should be replaced with an underscore `_` to keep naming consistent and eliminate the need to escape the filename in Linux.

I believe all files that contain the `°` symbol in the name should be changed to `deg` along with replacing the spaces with underscores `_`.

I can go into greater detail with my printer hardware and configuration and perform more thorough testing (once my printer is freed up) if needed, but wanted to document this asap in case someone else happened to be having the same issue.

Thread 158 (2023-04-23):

Clash of RA motor with MKS enclosure

sauravattri1, 2023-04-23:
I have found that for lower latitude version (20deg) of the OAT, the RA motor physically clashes with the [MKS bottom mounted case](https://wiki.openastrotech.com/en/OpenAstroTracker/Enclosures/Bottom_Mounted_MKS_Case).
As of now I only know of 20deg version(since I printed this one).
I have created another bottom mounted MKS case which is mounted to the rear of case that solves this problem.
I would suggest if there could be a heads up for people printing the bottom mounted MKS case that it is not physically compatible with lower latitude versions of the OAT.

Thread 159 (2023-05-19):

All latitude working

RY295, 2023-05-19:
Hi,  I live in bortle 9 skies and will travel to different dark places for astrophotography. I want  to use OAT with guiding, will it make a difference if I choose a 30 degree latitude or its mandatory that I make all latitude mod in OAT. I couldnt understand the modification required for all latitude instead of a fixed latitude say 30 degree. looking for help.
Thanks

ClutchplateDude, 2023-05-19:
I would print it for the highest latitude you expect to visit. Then for lower latitudes you will need to prop up the rear of the OAT by the difference between the highest and the current latitude.

You should pose questions like this in our Discord Questions forum, lots of people available to help there.

Closed 2023-05-19.

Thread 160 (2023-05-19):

Firmware for two motors for DEC axis

aamaya1969, 2023-05-19:
I would like to know how to configure firmware to use two motors on the DEC axis

ClutchplateDude, 2023-05-19:
This is not a support venue. Issues are reserved for bugs with the firmware.
Please use one of our support avenues, preferably Discord.

Closed 2023-05-19.

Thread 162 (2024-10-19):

FileNotFoundError: [Errno 2] No such file or directory

lynx2948, 2024-10-19:
[oat_fw_gui_2024-10-19-17-29-15.log](https://github.com/user-attachments/files/17447588/oat_fw_gui_2024-10-19-17-29-15.log)

The following Error message is diaplayed:
```
2024-10-19 17:37:45,098:CRITICAL:Exception caught
2024-10-19 17:37:45,098:CRITICAL:Traceback (most recent call last):
  File "shutil.py", line 815, in move
FileNotFoundError: [WinError 2] The system cannot find the file specified: 'D:\\Astronomy\\OpenAstro Tracker\\OATFWGUI_1.0.10-release+df7b94_Windows\\OATFWGUI_1.0.10-release+df7b94_Windows\\OpenAstroTech-OpenAstroTracker-Firmware-400a3cc' -> 'D:\\Astronomy\\OpenAstro Tracker\\OATFWGUI_1.0.10-release+df7b94_Windows\\OATFWGUI_1.0.10-release+df7b94_Windows\\OATFW'

During handling of the above exception, another exception occurred:

Traceback (most recent call last):
  File "D:\Astronomy\OpenAstro Tracker\OATFWGUI_1.0.10-release+df7b94_Windows\OATFWGUI_1.0.10-release+df7b94_Windows\OATFWGUI\qt_extensions.py", line 39, in run
    raise e
  File "D:\Astronomy\OpenAstro Tracker\OATFWGUI_1.0.10-release+df7b94_Windows\OATFWGUI_1.0.10-release+df7b94_Windows\OATFWGUI\qt_extensions.py", line 34, in run
    result = self.fn(*self.args, **self.kwargs)
  File "D:\Astronomy\OpenAstro Tracker\OATFWGUI_1.0.10-release+df7b94_Windows\OATFWGUI_1.0.10-release+df7b94_Windows\OATFWGUI\gui_logic.py", line 200, in download_and_extract_fw
    self.logic_state.fw_dir = extract_fw(zipfile_name)
  File "D:\Astronomy\OpenAstro Tracker\OATFWGUI_1.0.10-release+df7b94_Windows\OATFWGUI_1.0.10-release+df7b94_Windows\OATFWGUI\gui_logic.py", line 88, in extract_fw
    shutil.move(extracted_dir, fw_dir)
  File "shutil.py", line 835, in move
  File "shutil.py", line 434, in copy2
  File "shutil.py", line 254, in copyfile
FileNotFoundError: [Errno 2] No such file or directory: 'D:\\Astronomy\\OpenAstro Tracker\\OATFWGUI_1.0.10-release+df7b94_Windows\\OATFWGUI_1.0.10-release+df7b94_Windows\\OpenAstroTech-OpenAstroTracker-Firmware-400a3cc'
2024-10-19 17:37:45,098:CRITICAL:
```

This happen regardless of the firmware selected for down load.

Machine is running windows:
```
Edition	Windows 11 Home
Version	23H2
Installed on	‎10/‎1/‎2022
OS build	22631.4317
Experience	Windows Feature Experience Pack 1000.22700.1041.0
```

julianneswinoga, 2024-10-19:
Can you try moving the folder? There's a warning in the log:
```
2024-10-19 17:29:15,900:WARNING:Path D:\Astronomy\OpenAstro Tracker\OATFWGUI_1.0.10-release+df7b94_Windows\OATFWGUI_1.0.10-release+df7b94_Windows might
have too many characters in it (108)! Downloading/building firmware may create files with path
lengths greater than the default Windows path length of 260 characters.
If you get 'file not found' errors the easiest solution is to move
the D:\Astronomy\OpenAstro Tracker\OATFWGUI_1.0.10-release+df7b94_Windows\OATFWGUI_1.0.10-release+df7b94_Windows folder somewhere with less characters in the path.
```

lynx2948, 2024-10-20:
Restarted the OATFWGUI, loaded local config file, Selected 1.13.9 firmware and clicked download. Download completed successfully. selected MKS Gen L v1 clicked build FW. Build Firmware Completed successfully.

Closed 2024-10-20.

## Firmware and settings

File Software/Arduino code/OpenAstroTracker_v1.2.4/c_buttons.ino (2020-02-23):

void loop() {

  if (adc_key_in < 1000) delay(150);
  lcd_key = read_LCD_buttons();
  //speedcalibration += inputcal / 1000;
  float trackingspeed = ((((335.1417 / 24) / 12) * RevSteps) / 3590) - 1 + float(speedcalibration);

  float onehour = RevSteps * ((RAsteps) / 288);
  moveRA = (hourRA * onehour + minRA * (onehour / float(60)) + secRA * (onehour / float(3600))) / 2;
  moveDEC = (degreeDEC * float(164) + minDEC * (float(164) / float(60)) + secDEC * (float(164) / float(3600))) / 2;

  if (moveRA > (6 * onehour / 2)) {         //turn both RA and DEC axis around if target is below horizontal parallel
    moveRA -= long(12 * onehour / 2);
    moveDEC = -moveDEC;
  }
  if (moveRA < (-6 * onehour / 2)) {         
    moveRA += long(12 * onehour / 2);
    moveDEC = -moveDEC;
  }

  stepperRA.moveTo(-moveRA);
  stepperDEC.moveTo(moveDEC);

  switch (lcd_key) {
    case btnUP: {
        while (menu == 0) {
          if (RAselect == 0) hourRA += 1;
          if (RAselect == 1) minRA += 1;
          if (RAselect == 2) secRA += 1;
          break;
        }
        while (menu == 1) {
          if (DECselect == 0) degreeDEC += 1;
          if (DECselect == 1) minDEC += 1;
          if (DECselect == 2) secDEC += 1;
          break;
        }
        while (menu == 2) {
          if (HAselect == 0) hourHA += 1;
          if (HAselect == 1) minHA += 1;
          break;
        }
        while (menu == 5) {
          inputcal += 1;  //0.0001;

          break;
        }
        break;
      }

    case btnDOWN: {
        while (menu == 0) {
          if (RAselect == 0) hourRA -= 1;
          if (RAselect == 1) minRA -= 1;
          if (RAselect == 2) secRA -= 1;
          break;
        }
        while (menu == 1) {
          if (DECselect == 0) degreeDEC -= 1;
          if (DECselect == 1) minDEC -= 1;
          if (DECselect == 2) secDEC -= 1;
          break;
        }
        while (menu == 5) {
          inputcal -= 1 ; //0.0001;

          break;
        }
        //while (menu == 2) {
        //  break;

        /*while (menu == 4) {              // only counting up recommended, breaks code otherwise
          if (HAselect == 0) hourHA -= 1;
          if (HAselect == 1) minHA -= 1;
          break;
          }*/
        break;
      }

    case btnSELECT: {
        /*stepperRA.moveTo(-moveRA);
          stepperDEC.moveTo(moveDEC);*/
        if (menu < 2) {
          while (stepperRA.distanceToGo() != 0  && stepperDEC.distanceToGo() == 0) {
            stepperRA.run();
          }
          while (stepperDEC.distanceToGo() != 0 && stepperRA.distanceToGo() == 0) {
            stepperDEC.run();
            stepperTRK.setSpeed(trackingspeed);
            stepperTRK.runSpeed();
          }
          while (stepperDEC.distanceToGo() != 0 || stepperRA.distanceToGo() != 0) {
            stepperRA.run();
            stepperDEC.run();
          }
        }

        if (menu == 3) {
          hPolarisPosition = 2 - hourRAprint;
          mPolarisPosition = 57 - minRAprint;
          if (mPolarisPosition < 0) {
            hPolarisPosition -= 1;
            mPolarisPosition += 60;
          }
          if (hPolarisPosition < -6) {
            hPolarisPosition += 24;
            stepperDEC.moveTo(213.4);
          }
          else stepperDEC.moveTo(-213.4);

          if (hPolarisPosition > 6) hPolarisPosition -= 12;
          int hPolarisMoveTo = (hPolarisPosition * onehour + mPolarisPosition * (onehour / 60)) / 2 ;
          stepperRA.moveTo(-hPolarisMoveTo);   //             (float(4096) / float(60)));    alt

          while (stepperRA.distanceToGo() || stepperDEC.distanceToGo() != 0) {
            stepperRA.run();
            stepperDEC.run();
          }
        }

        if (menu == 4) {
          if (heatselect == 0) {
            RAheat += 1;
            if (RAheat > 1) RAheat = 0;
          }
          if (heatselect == 1) {
            DECheat += 1;
            if (DECheat > 1) DECheat = 0;
          }
          break;
        }
        if (menu == 5) {

          EEPROM.update(0, inputcal);
          break;
        }
        break;
      }


    case btnLEFT: {
        if (menu == 0) {
          RAselect += 1;
          while (RAselect > 2) RAselect = 0;
          break;
        }
        if (menu == 1) {
          DECselect += 1;
          while (DECselect > 2) DECselect = 0;
        }
        if (menu == 2) {
          HAselect += 1;
          while (HAselect > 1) HAselect = 0;
          break;
        }
        if (menu == 4) {
          heatselect += 1;
          while (heatselect > 1) heatselect = 0;
        }
        break;
      }

    case btnRIGHT: {
        menu += 1;
        while (menu > 5) menu = 0;
        break;
      }
  }

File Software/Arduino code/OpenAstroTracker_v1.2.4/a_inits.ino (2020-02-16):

// If you really want to look through this code, i apologise for my terrible coding
//#include <SoftwareSerial.h>
#include <EEPROM.h>
#include <AccelStepper.h>
#include <LiquidCrystal.h>
#define HALFSTEP 8
#define FULLSTEP 4
LiquidCrystal lcd(8, 9, 4, 5, 6, 7);

#define motorPin1  2    // IN1 auf ULN2003 driver 1
#define motorPin2  3    // IN2 auf ULN2003 driver 1
#define motorPin3  11    // IN3 auf ULN2003 driver 1
#define motorPin4  12    // IN4 auf ULN2003 driver 1

#define motorPin11  15    // IN1 auf ULN2003 driver 2
#define motorPin12  16    // IN2 auf ULN2003 driver 2
#define motorPin13  17    // IN3 auf ULN2003 driver 2
#define motorPin14  18    // IN4 auf ULN2003 driver 2

#define btnRIGHT  0
#define btnUP     1
#define btnDOWN   2
#define btnLEFT   3
#define btnSELECT 4
#define btnNONE   5

int lcd_key     = 0;
int adc_key_in  = 0;
int read_LCD_buttons() {
  adc_key_in = analogRead(0);
  if (adc_key_in > 1000) return btnNONE;
  if (adc_key_in < 50)   return btnRIGHT;
  if (adc_key_in < 250)  return btnUP;
  if (adc_key_in < 450)  return btnDOWN;
  if (adc_key_in < 600)  return btnLEFT;
  if (adc_key_in < 920)  return btnSELECT;
  //return btnNONE;
}

String inString = "";


AccelStepper stepperRA(FULLSTEP, motorPin1, motorPin3, motorPin2, motorPin4);
AccelStepper stepperDEC(FULLSTEP, motorPin11, motorPin13, motorPin12, motorPin14);
AccelStepper stepperTRK(HALFSTEP, motorPin1, motorPin3, motorPin2, motorPin4);     //yes, this is the same motor as stepperRA, dont ask why
AccelStepper stepperGUIDE(HALFSTEP, motorPin1, motorPin3, motorPin2, motorPin4);

String inCmd;
//String inputString = "";
//String commandString = "";
//boolean isConnected = false;

String logString;
//boolean stringComplete = false;
//unsigned long timeWait;
boolean isPulseGuiding = true;

unsigned long Zeit;

boolean pcControl = false;
int menu = 2;
int currentSecs;
int currentMins;
float inputcal;
float speedcalibration;
int direction_old = 1;
int direction_new;

int hPolarisPosition;
int mPolarisPosition;

int tracking = 1;

//RA stuff
float hourRA;
float minRA = 0;
float secRA = 0;
float moveRA;
int RAselect;
int hourRAprint;
int minRAprint;

//DEC stuff
int degreeDEC;
int minDEC;
int secDEC;
float moveDEC;
int DECselect;

//Hour correction
int hourHA = 0;
int minHA = 0;
int HAselect;
int hHAcorrection;
int mHAcorrection = -5 ;  //wenn minus dann hHAcorrection -1
int sHAcorrection;
int hourHAzeit;
int minHAzeit;

int heatselect;
int RAheat = 0;
int DECheat = 1;


byte DEG[8] = {
  B01100,
  B10010,
  B10010,
  B01100,
  B00000,
  B00000,
  B00000,
  B00000
};

byte min[] = {
  B10000,
  B10000,
  B10000,
  B00000,
  B00000,
  B00000,
  B00000,
  B00000
};

byte sec[] = {
  B10100,
  B10100,
  B10100,
  B00000,
  B00000,
  B00000,
  B00000,
  B00000
};

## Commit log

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2020-03-21 Menu improvements. Up/Down support in HA.
    Added a custom character for menu highlighting.
    Selected menu item is now always center screen.
    HA adjustments supports Up and Down and correctly wraps around.
    [a_inits.ino, c_buttons.ino, e_printout.ino]
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2020-03-21 Used constants for menu names. Formatting and bug fix.
    Menus can be referred to by name now.
    Formatted new code I'd added to use the coding style already present.
    Fixed a overflow error in the HA Menu's Up button processing.
    [a_inits.ino, c_buttons.ino, e_printout.ino]
2020-03-23 LCD menu, DayTime class, CTRL menu
    Added LCD Menu class to handle menu display, switching, etc.
    Added DayTime class to handle adding and subtracting time while correctly handing over and underflow.
    Replaced HA and RA with DayTime class as a first attempt.
    Added CTRL menu that allows moving both axes in both directions without changing time settings.
    Debounced menu keys that make single choices.
    Moved delay on keypress into each keypress case, since some needed to not delay.
    Added status to LCD while in a stepper loop.
    Moved writing HA to EEPROM to where HA menu is left (need to add check whether it's changed).
    [a_inits.ino, c_buttons.ino, d_calculations.ino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]
2020-03-24 Refactoring, utility funcs, simplification, bug fixes
    Added logging functions.
    Moved stepper motor target calculations into its own file. Added comments.
    Used DayTime class for RATime and HATime.
    Ensured RATime works correctly.
    When moving an axis, the LCD displays progress via percent complete.
    Fixed bug in LCD menu functions that didn't correctly print floats and caused a hang (!).
    Re-added the old calculation code to verify new code works teh same way.
    [a_inits.ino, c_buttons.ino, d_calculations.ino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]
2020-03-25 Major refactor
    - Moved each menu into their own file
    - Moved utitlity functions into their own file
    - Created functions to handle key processing and display in those files
    - Added CTRL menu to allow free movement of the steppers (and to calibrate to zero point (celestial pole)). Use SELECT/LEFT to start moving RA, UP/DOWN to start moving DEC, click again to stop)
    - Added HOME menu to return to zero point (celestial pole)
    - Made CAL input speed up the longer you hold it down
    - Made HEAT menu optional
    - Added 'splashscreen' on startup
    - Allowed some debug code to be excluded from compilation
    - Fixed tracker stepper not being stepped all the time
    - Added some limits to stepper movements to prev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
    [a_inits.ino, c_buttons.ino, d_calculations.ino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]
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2020-03-26 Fixed some key processing bugs
    - Keys were being waited on when they shouldn't
    - Placed all the vararg stuff in the DEBUG mode (seems flaky).
    - DEC movement did not display progress.
    [c_buttons.ino]
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2020-03-29 V1.5.10 - Updates
    - Commented out all existing Serial code.
    - Added basic Meade protocol support (WIP). Totally untested, since I don't have a way to test it ATM.
    - Made sure logString doesn't consume oodles of memory.
    - Updated the PC app to use the Meade protocol commands.
    [a_inits.ino, c_buttons.ino]
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2020-03-30 V1.5.20 - Updates
    - Fixed a bug in time handling (affected HA loading)
    - Home menu now takes travelled tracker distance into account and adjusts HA time accordingly.
    - Removed Polaris menu and added Polaris as the first Point of Interest.
    - Added new INFO menu to show stepper motor positions, version number and any other info that seems needed.
    - Removed some of the magic numbers in the stepper calculations that seemed unnecessary.
    - Renamed some variables to better describe their meaning.
    - Added general comments as well as comments explaining the math behind calculating the RA and DEC steps.
    - Changed the RASteps value substantially (from 330 to 300) in accordance with the math of the har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
    [a_inits.ino, c_buttons.ino]
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2020-04-01 V1.5.22 - Updates (Code size optimization)
    - Made display updates while slewing time-based (instead of cycles).
    - Changed all ints to bytes that I could to save data storage.
    - Optimized a lot of string manipulation that was using String class to use sprintf() on a new scratch buffer instead.
    - Changed the menu system to use an array instead of a linked list to save memory.
    - Removed all vararg based calls (too much utility code).
    - Disabled tracking during homing slew.
    - Changed Meade :Q# command to simply stop motors (not tracking), but not exit Control mode.
    - Changed Meade :Qq# command to exit Control mode, but not stop motors.
    [a_inits.ino]
2020-04-03 V1.5.24 - Updates
    - Implemented current RA and DEC query in Meade protocol.
    - Fix bug in Serial setting HA Meade command. Now returns 0.
    - Implemented Park command to stop all movement (including tracking) after returning to home position.
    - Removed custom protocol on Serial port to avoid code duplication and reduce code size.
    - Removed the stepperGUIDE instance since it was not being used and there's no space for multiple protocols.
    - Made the Home command correctly update RA and HA so that you can continue working without resetting everything.
    - Made RA movement asynchronous like DEC.
    [a_inits.ino]
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2020-04-05 V1.6.01 - Updates
    - Fixed pin assignment on DEC
    - Moved key handling to its own class
    - Added target and current values for RA and DEC to INFO menu
    - Enabled and fixed Serial code.
    - Fixed some misnamed variables in the Mount class
    [a_inits.ino, c_buttons.ino]
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2020-04-06 V1.6.10 - Updates
    - Placed all Serial output, except Meade Protocol implementation inside a DEBUG_MODE define
    - Removed a bunch of logging/commented out code.
    - Correctly implement current RA and DEC retrieval.
    [c_buttons.ino]
2020-04-06 V1.6.11 - Updates
    - Turns out the DEC stepper was reversed. Fixed.
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2020-04-06 V1.6.13 - Updates
    - Fixed a bug that was display RA and DEC instead of the stepper motor steps in the CTRL menu.
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2020-04-10 V1.6.17 - Updates
    - Made calibration use two bytes for storage, so you can set adjust more than a factor 1.0255
    - Renamed the Polaris RA coordinates.
    - Forced users to choose the correct RA ring before compiling.
2020-04-10 V1.6.19 - Updates
    - Moved Firmware configuration information to Globals.h since Arduino IDE does not include .ino files when compiling C++ files.
    - Default firmware configuration is to include everything except Serial (and HEAT, cause that's broken).
    - Removed a bunch of commented out debugging code.
    - Made the LCD now constantly display RA and DEC when in Serial control mode (SELECT still exits).
    - All Meade commands now return a 0 or 1 to indicate failure or success.
    - Removed the logging string collection from Serial because we are so memory constrained already, that logging is a luxury we can't afford.
    [a_inits.ino, c_buttons.ino]
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2020-04-10 Driver Updates
    - Didn't realize VB uses spaces instead of tabs in my last commit.
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2020-04-13 V1.6.20 - Updates
    - Added some missing Serial commands for the ASCOM driver (Unpark, SlewSync, and GetSlewing)
2020-04-14 STL Updates - Adjustable motor mounts
    I remixed the RA and DEC mounts to allow adjustment of the stepper position so you can remove all slop from the belts. Especially useful when you take the system out into the cold and everything shrinks a little.
    [11_DECMountBracketAdjstble.stl, 14_RAMountBrcktAdjstble.stl]
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2020-04-15 ASCOM 0.1.3.0 RC1
    Fix some CONFORM issues, Add SYNC functionality, add ReadMe, Conformance report, Setup EXE, and spreadsheet of ASCOM functionality.
    [ASCOM Methods and Properties.xlsx]
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2020-04-18 ASCOM Driver 0.1.4.1b
    Fixes issue handling return value from halt, updates Conformance test results
2020-04-20 V1.6.32 - Updates
    - Added support for Drift Alignment in the CAL menu.
    - Changed default client to not include INFO menu (memory pressure - can be enabled is GUIDED_STARTUP is disabled).
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2020-04-25 V1.6.35 - Updates
    - Switched to VIsual Studio for development. Arduino IDE should still function correctly.
    - Optimized menu display updates to LCD (performance improvement).
    - Reformatted some source code for consistency.
    - Added some const-correctness attributes.
    [a_inits.ino, c_buttons.ino]
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2020-04-27 V1.6.36 - Updates
    - Added new X class of commands to Serial.
    - Added :XDsss# command to perform Drift alignment in the number of seconds specfiied
    - Added :hF# command to move the mount to the home position (same as Park, but does not stop tracking).
    - Added :SHP# command to set the current location as the home location.
    - Added :SHLhhmmss# command to set the current Local Sidereal Time.
2020-04-29 V1.6.37 - Updates
    Fixed a bug in LCD button test
    [c_buttons.ino]
2020-04-30 Fixing WiFi Control, using defines where needed, fixing stepper for ESP8266
    [a_inits.ino, c_buttons.ino]
2020-05-01 fixing boards.
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2020-05-20 fix parts 06a,c
    [06a_splitring_part1_v4.STL, 06c_splitring_part3_v4.STL]
2020-05-22 V1.6.50 - WIP Updates
    - Added yield() calls (ESP8266 board has a watchdog that resets if the code blocks for more than a few seconds).
    - Refactored HA/LST handling.
    - RA and DEC are now always updated and calculated according to stepper motor positions
    - Changed EEPROM writing code to only write if the value changed.
    - Added ability to slew by setting a speed for each axis.
    - Added Serial command: :Mc# - starts slewing in the direction specified by 'c'
    - Added Serial command: :XGH# - gets the HA
    - Added Serial command: :XGL# - gets the LST
    - Added Serial command: :XSMn# - set manual continuous slewing mode
    - Added Serial command: :XSXn.nnn# - set continuous slewing mode RA speed
    - Added Seri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
2020-05-22 fix for a older part
    [14_RAmotor_mount_low_200x200.STL]
2020-05-22 Revert "fix for a older part"
    This reverts commit a434e5244c4369af2294426812b365207f4d15b9.
    [14_RAmotor_mount_low_200x200.STL]
2020-05-23 V1.6.51 - Updates
    - FIxed a bug that was preventing correct EEPROM reads.
    - Removed a redundant menu active item variable.
    - Fixed a crash caused by a switch statement (compiler bug?).
    - Added and removed some debug logging statements.
    - Changed LCD display to display RA and DEC coordinates instead of stepper position.
    [a_inits.ino, c_buttons.ino]
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2020-05-24 V1.6.52 - Updates
    - Fixed key handling, which was suffering from some race-like conditions.
    [c_buttons.ino]
2020-05-25 V1.6.54 - Updates
    - Changed Sync command on Mount to sync both coordinates at the same time, since individual syncs cause issues (related to flipping).
    - Go Home command is now asynchronous.
    [a_inits.ino]
2020-05-25 Added option to reverse RA and DEC motor direction.
    [a_inits.ino]
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2020-05-28 V1.6.55 - Updates
    - Added support for backlash compensation. When slewing west, it will overshoot by a few steps (16 by default) and then slew east those sixteen at the end of the slew. Not that this is only done for targeted slews.
    - Meade command extension :XGB# and :XSB# added which returns and sets, respectively, the number of backlash steps to take.
    - Slewing to Home wasn't working correctly. FIxed.
    - Increased mount status output to every 2s instead of every second.
    - Added ToString() utiltity functions to DayTime and DegreeTime
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2020-06-01 OATControl V0.9.3.0 Updates
    - Improved readability of Chooser dialog.
    - Fixed name display of discovered Wifi devices.
    - Fixed a cross-thread bug for discovered Wifi devices
    - Added Rescan button to Device Chooser dialog.
2020-06-02 V1.6.57 - Updates
    - Fixed a bug where negative time was displayed incorrectly.
    - Fixed a bug in Set Home that did not account for current RA position.
    - Fixed a bug that incorrectly calculated current RA from stepper position.
    - Added some logging for debugging.
2020-06-03 V1.6.58 - Updates
    - Fixed DEC pin definitions
    - Added new Serial command :XGN# that gets the network settings (if there's a ESP8266 board with a WiFi connection)
    - Fixed the bug that was causing inverted RA (e.g. 12hr offset in Stellarium)
    [a_inits.ino]
2020-06-03 V1.6.59 - Updates
    - Corrected the DEC pin order to correspond to the wiring diagram for the Mega
    [a_inits.ino]
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2020-06-06 V1.6.60 - Updates
    - Fixed a bug in the Go Home function that did not reset the RA target value.
    - Added support for setting backlash steps in the CAL menu.
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2020-06-07 V1.6.61 - Updates
    - Updated Meade inline documentation of supported command set.
    - Added support for setting and getting Lat/Long of the mount.
    - Reversed stepper direction to RA and TRK in southern hemisphere.
2020-06-08 V1.7.00 - Updates
    - Southern hemisphere support is now working correctly.
    - Swapped DEC motor pins 2 and 3 for ESP8266.
    [a_inits.ino]
2020-06-08 V1.7.01 - Updates
    - Fixed stepper configuration for northern and southern hemispheres.
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2020-06-13 V1.7.04 - Updates
    - Fixed a bug that prevented the speed calibration factor adjustment to persist correctly.
    - Fixed a bug that did not adjust the tracking speed as you increased the speed calibration factor
2020-06-14 fix part 14
    [14_RAmotor_mount_v4.STL, 14_RAmotor_mount_v5.STL, 22_RAmotor_mount_v4.SLDPRT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]
2020-06-15 fix for 04_rollmount_2020base not having holes
    [04_rollmount left_20°_v4_2020base.SLDPRT, 04_rollmount left_20°_v4_2020base.STL, 04_rollmount left_20°_v4_2020base.step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]
2020-06-15 Added ESP32, fixed definitions not being recognized because of missing library dependency finder configuration see https://docs.platformio.org/en/latest/librarymanager/ldf.html#dependency-finder-mode
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2020-06-18 ESP - Updates
    Interrupt changes - attempts to stabilize the code according to https://docs.espressif.com/projects/esp-idf/en/latest/esp32/api-reference/storage/spi_flash.html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
2020-06-18 fixed esp32 compilation
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2020-06-19 V1.7.12 - Updates
    - Converted all logv() calls to LOGVn() calls that compile out, but don't need to enclosed in #if..#endif statements
    - Fixed a bug introduced in 1.7.11 that prevented normal functioning of the OAT steppers.
2020-06-20 OATControl V0.9.7.0 - Updates
    - Added Polar Alignment function
    - Replaced slider for manual slew speed with 4 different slew rate buttons (1-4, 1 is slowest, 4 is fastest). Manual Arrow slewing and virtual joystick slewing respect this selection.
    - Made some minor cosmetic changes in the OAT Chooser
2020-07-02 V1.7.14 - Updates
    - Fixed a bug in Polar Alignment (this never actually worked correctly)
    - Fixed a bug in the Sync function of the mount
    - Added backlight adjustment, but it does not work (crashes the board), so it is commented out. Might revisit later.
2020-07-06 V1.7.15 - Updates
    - Fixed the EEPROM persistence failures on ESP boards.
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2020-07-14 Fix current_RA not being calculated right for NEMA steppers
2020-07-19 1.7.21b
    * Add reverse Motor function for NEMA
    * fix guidespeed for NEMA steppers
    * add sidereal calculations from neo6m module (doesnt work yet)
    * more menu cleanups
    *
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2020-07-25 update poles and polemount
    * poles to v3
    * polemount to v2
    [03_polemount_6801.SLDPRT, 03_polemount_6801.STL, 03_polemount_6801.step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]
2020-07-31 V1.7.29 - Updates
    - Fixed startup issue with incorrect HA handling.
    - Changed RA and DEC display to indicate whether displaying target or current coordinates with the ability to switch between the two
    - Commented out all verbose mount logging to reclaim some heap memory.
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2020-08-01 V1.8.01 - Updates
    - Updated Platform.IO to use correct libraries
    - Removed some old code from startup
    - Defaulted to no drivers for steppers
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2020-08-02 V1.8.03 - Updates
    - Fixed incorrect driver setting for default steppers
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2020-08-05 V1.8.05 - Updates
    - Reverted Headless mode to off
    - Increased screen updates back to 5Hz.
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2020-08-06 V1.8.06 - Updates
    - DEC axis was inadvertently inverted by default after merge. Fixed.
    - Guide pulses were not 2x sidereal and 0 for default steppers. Fixed.
2020-08-08 V1.8.10 - Updates
    - Permanent display of tracking state in top-right corner of display.
    - Shortened menu display
    - Full GPS module (GT-U7) support for LST and location
    - Separated HA menu into two files (one for GPS support, one for non-GPS)
    - Added display of current location to INFO menu
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2020-08-09 V1.8.12 - Updates
    - Temporary fix for compile error from 1.8.11
    - add different MS modes for DEC slewing/guiding
    - add UART "noisefeedback" to config
    - hardcoded guidemultipliers for 28by
    - stop tracking during a slew with NEMAs to prevent inaccurate slews
2020-08-09 DigitalLevel Addon
    Added the CAD/STL files and a readme for the digital level.
    [Digital Level Holder Cable Clamp.stl, Digital Level Holder v7.f3d, Digital Level Holder v7.step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]
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2020-08-09 V1.8.14 - Updates
    - Turned the power to the Azimuth and Altitude motors on and off as needed.
    - Enabled Altitude correction from LX200 commands
    - Prevented tracking from starting after parking for NEMA motors.
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2020-08-10 V1.8.15 - Updates
    - Fixed linker error in ESP32 build.
2020-08-10 AutoPA scripts initial upload
    Python scripts that calculate polar misalignment values based on three RA/DEC inputs. It determines the alt/az of the current alignment, calculates the delta compared to true polar alignment, then issues LX200 commands to the OAT to correct.
2020-08-11 AutoPA Updates
    Added calibration script and some bug fixes.
2020-08-11 V1.8.16 - Updates
    - Throttled the INFO display update frequency (it was updating every cycle before).
    - Added temperature display when using the Digital Level module
    - Made the axis swap for the DIgital Level on by default since most people will use the STL in the repo for the holder.
2020-08-12 Holder for the GPS antenna
    Can also hold the driver board for the Altitude motors.
    [GPS Antenna Holder.stl]
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2020-08-13 Improved Guider
    minor corrections
    [camera_lid.stl, camera_mount.stl, front.stl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]
2020-08-14 V1.8.19 - Updates
    - Azimuth motor control during Polar Alignment was not implemented.
    - After confirming Polar Alignment, the display shows slewing activity and no longer switches to the INFO menu.
    - Pressing Right Button while slewing home after Polar Alignment now stops the slewing before changing menus.
    - Removed some logging
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2020-08-18 V1.8.20 - Updates
    - Azimuth and Altitude motor state in LX200 GX command was only updating their status while slewing. Fixed.
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2020-08-31 Fixed compiler issue for TMC uart drivers and nema motors
2020-09-09 Fix wormgear cap scaling
    [Alt_wormgear_cap.stl, Alt_wormgear_cap_V2.stl]
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2020-10-04 V1.8.25 - Updates
    - Added special char for Tracking display on LCD.
    - Renamed some conflicting defines (HALFSTEP et al to HALFSTEP_MODE)
    - Moved all Debug strings to Flash memory
    - Simplified EEPROM class (made it all static)
    - Added prompt when pressing SELECT in either Roll or Pitch display in CAL menu, whether to save the reference value
    - Fixed ESP32 compilation problem in freeMemory() implementation
2020-10-05 V1.8.30 - Updates
    - Fixed a bug that turned off Tracking when you tried to slew RA to the current location
    - Improved some comments
    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
2020-10-05 Fixed a platform io build error on linux due to case sensitivity of the board name
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2020-10-08 6801 bearing for rear mount
    Alternate rear mount to use 6801 bearing instead of 625.
    [13_rear_AltAz_mount_6801.step, 13_rear_AltAz_mount_6801.stl, 6801_5mm_bushing.step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]
2020-10-08 Fix 625 rear mount
    [13_rear_AltAz_mount.step, 13_rear_AltAz_mount.stl]
2020-10-08 V1.8.33 - Updates
    - fixed a bunch of typos that massively screwed up DEC guiding
2020-10-09 The Monster enclosure
    Added my STL files for this enclosure. Sorry I don't use any CAD programs that produce STEP or F3D files...
    [ButtonDown.stl, ButtonLeft.stl, ButtonReset.stl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]
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2020-10-10 Update part 11 DEC motor mount for NEMAs
    Now fits square NEMA17
    [11_DEC_motor_mount_NEMA14.STL, 11_DEC_motor_mount_v9_NEMA.STL, 16_DEC_motor_mount_v8_low_NEMA14.SLDPRT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]
2020-10-11 Astroberry All-in-One Box
    Electronics box designed to house an Arduino Mega, RPi4, multiple buck converters, a powered USB hub, and space for more.
    [Back Cover.step, Back Cover.stl, Box Divider.step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]
2020-10-15 V1.8.39 - Updates
    - Fixed guiding to not jump back and forth on pulses.
    - Fixed tracking during slew. We now turn off tracking for slew and compensate at the end of the slew.
    - Fixed type for DEC motor speed.
    - Added M33 and Pleiades to GO menu.
    - Added lots of debug output around stepper motor control under new macro DEBUG_STEPPERS
2020-10-15 V1.8.40 - Updates
    - Fixed RA negative movement, which was not switching to Slew microstepping settings.
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2020-10-16 Fix for button reset loop
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2020-10-18 V1.8.42 - Updates
    - Fixed bug that turned of tracking when using NEMA17 with a non-UART driver.
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2020-10-31 V1.8.45 - Updates
    - Fixed some ESP32 build errors
    - Checked from some invalid ESP32 configurations
    - Corrected some Meade command comments
    - Sorted GO targets alphabetically (except Polaris)
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2020-11-20 Fix softwareserial driver configs
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2020-11-24 V1.8.52 - Updates
    - Moved LCD updates out of the mount loop.
    - Fixed a bug that did not correctly handle displaying Roll and Pitch offset.
    - Added ability to define DEC limits. Limits are not enforced yet, that code is still in development.
    - Added new debug channel for digital level.
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2020-11-26 ESP32 Build Fix
2020-11-27 HardwareSerial for ESP
    -Only use HardwareSerial for ESP32 boards.
    -Minor bugfixes.
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2020-11-28 V1.8.60 - Updates
    - Rewrote the coordinate handling to correctly handle negative coordinates between 0 and -1.
    - Prevented backlash code from doing nothing when backlash is zero.
2020-11-30 V1.8.61 - Updates
    - Fixed some bugs in the coordinate handling.
    - Added some more logging.
    - Removed an errant Meade return value when no command was sent.
    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
2020-11-30 V1.8.62 - Updates
    (Numbers are off because git)
    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
2020-12-05 LCD Pin configuration fix
2020-12-05 Revert "LCD Pin configuration fix"
    This reverts commit 06bbc9a574fc6107e53a638ad0bac90f7c2cc5b5.
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2020-12-23 Repository cleanup
    - removed Software (moved to separate repos)
    - removed Addons (moved to separate repos)
    [01_camera_mount_v2.SLDPRT, 01_camera_mount_v2.STL, 01_camera_mount_v2.step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]
2021-01-10 CAD & STL cleanup
    Reorganized CAD files, Assigned correct numberation, reexprted some STLs to correct resolution and orientation
    [00_calibration.SLDPRT, 00_calibration.step, 01a_Baseplate_part1.SLDPRT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]
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2021-04-25 fix RA wheel for 200x200 printers
    [06a_splitring_part1_v4_200x200.SLDPRT, 06a_splitring_part1_v4_200x200.STL, 06a_splitring_part1_v4_200x200.step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]
2021-05-13 Added my DEC mount with idler support. Requires 2 x 2mm steel rods and 2 x GT2 idlers with 5mm shaft on bearings.
    [11_DEC_motor_strong_mount_w_idlers_NEMA.STL]
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2021-06-04 fix 05_pole_v5
    [05.2_stabilizer.SLDPRT, 05_pole_v5.SLDPRT, 05_pole_v5.STL]
2021-06-11 fix 05 pole
    had too big holes
    [05_pole_v5.SLDPRT, 05_pole_v5.STEP, 05_pole_v5.STL]
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2021-10-29 add parts for Threaded Inserts
    Added alternative parts with the postfix "_TI" for the use of M3x4.6x6mm Threaded Inserts:
    - Rollmounts
    - Polemount
    - Poles
    - RA Ring
    - DEC bearing holder
    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
    [02_angle_50deg_v4_2020base.SLDPRT, 03_polemount_6801_v2.SLDPRT, 03_polemount_6801_v2.STL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]
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
